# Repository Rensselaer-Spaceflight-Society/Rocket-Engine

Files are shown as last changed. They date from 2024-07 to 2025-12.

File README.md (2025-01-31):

# RPU Systems Design and Communications Protocol V1.1.0

> [!IMPORTANT]
> Last Updated: 10/8/2024

Below is a brief overview of the design and communications protocol between our laptop acting as our remote interface (i.e. the control room) and the Rocket Engine Test Stand itself.

## Table of Contents

- [Control Room](#control-room)
- [Test Stand Controller](#test-stand-controller)
- [Powering the Test Stand](#powering-the-test-stand)
- [Sensors](#sensors)
- [Valves](#valves)
- [Communications](#communications)
- [Command and Control](#command-and-control)
- [Sensor Data Transfer](#sensor-data-transfer)
- [Control Flow](#control-flow)
- [Arduino Pinout](#arduino-pinout)
- [Additional Info](#additional-info)

## Control Room

The software that remotely monitors the engine and allows us to send commands to the engine. This software is responsible for:

- Countdown
- Receiving and Saving Data
- Hold and Abort Signals
- Displaying the Data in a Human Friendly Way
  - Charts
  - Text Outputs
  - Color coding for if data is out of spec

### Technologies

We are using C++ and Qt 6.7.2 to build the control room software. You can install the Qt framework for Open Source Usage from https://www.qt.io/download-open-source.

## Test Stand Controller

The rocket engine controller is an Arduino based platform that controls the physical aspects of the rocket engine. This was the primary focus for the semester and is still the primary focus for this summer. This software is responsible for:

- Reading Sensors
- Opening and Closing Valves
- Sending Sensor Data back to the Control Room
- Ignition and Shutoff Sequence
- Processing Control Signals

## Powering the Test Stand

We have a variety of electronics that need power:

- Solenoid Valves, 48W (12vdc @4A)
- Arduino, 1W (12vdc @0.08333)
- Sensors, 5W (5v @1A)

The sensors need 5v, but everything else needs 12v, fortunately, the Arduino's power regulation will step the power down to 5v for the sensors.

Its really hard to send 60w @ 12vdc over 300ft, so we decided that battery power is our best bet for powering the test stand. Lithium Iron Phosphate (LiFePO4) batteries show the best potential for delivering both the voltage and current that the test stand will need.

The use of battery power allows us to set our downrange distance anywhere from 300ft (100m) - 3400ft (1000m).

### Technologies

This is built on the Arduino platform for easy and plentiful I/O. Arduino provides plenty of digital and analog pins for reading sensors and controlling valves. It also provides simple serial communications over UART.

> [!NOTE]
> Originally the rocket engine was supposed to be controlled via Raspberry Pi, we switched to the arduino platform for a couple reasons.
>
> - Setup is easier as there is no need to ssh into the arduino and run the control program, it starts up automatically on power on.
> - The Raspberry Pi has no Analog pin headers, the pressure transducers are analog sensors, switching to Arduino removes the need for analog-digital converters.
> - The Arduino takes less power, we can power it really easily via the VIN and GND pins compared to RasPI which is much harder to power
> - Arduino has first class support for our serial communications, where as raspberry pi has support but is slightly more difficult to implement
> - Arduino has no OS that is also has to run, it just runs our code and our code only.

## Sensors

The rocket engine has 8 sensors:

- 1 Load Cell for measuring thrust
- 4 Thermocouples
    - 1 At the Nozzle exit
    - 1 On the Kerosene Inlet and Injector Plate
    - 1 On the N2O inlet and injector Plate
    - On the combustion chamber at the throat of the nozzle (the constriction)
- 6 Pressure Transducers
  - 1 Inside the Combustion Chamber
    - According to David, the back of the combustion chamber should be cool enough to not destroy this sensor
  - 1 Down Line of the Inert Gas System
  - 2 Before the injector plate
    - 1 for fuel
    - 1 for oxidizer
  - 2 After the valves for fuel and oxidizer

The pressure transducers are analog sensors that vary their voltage depending on the pressure they are detecting.

The thermocouple and load cell both have amplifiers that act as analog-digital converters. The signals we take in will be digital signals. The thermocouple unfortunately does work on SPI (sorry Ashton).

## Valves

We are using three 12v solenoid valves that operate at 1.33 amps. This is simply too much power to send over a wire with our budget. See the power section for more information.

Power will be delivered to the solenoids via solid-state relays, this allows the
5v logic level of the Arduino power the relays reliably.

## Communications

The goal is to not be anywhere close to the engine when it is firing, the team is still deciding on an acceptable distance, but the current number is between 50 - 100m (170 - 340ft). To achieve this range with easy and reliable communications we are using UART serial communications via ethernet. This provides a well supported, and robust communication method.

> [!IMPORTANT]
> The Baud Rate for the serial communications has yet to be finalized, for testing we are using 9600 but this may change in the future.

Specifically the serial data will be converted to RS485 and sent over Cat 5 ethernet cable, this is supposedly an effective way to handle long range wired communication. [Source](https://electronics.stackexchange.com/questions/113188/long-distance-communication)

The Arduino's serial communication library automatically handles parity, start, and stop bits, so we don't need to handle this necessarily. The default is 8 data, 1 start and 1 stop bit with no parity, but we may be able to change this if needed.

Communications should be handled over the the Serial1 Port on the Arduino, Serial0 (aka just "Serial) is reserved for debugging via the Serial Monitor.

## Command and Control

The control room and the test stand use 64 bit (8 byte) signals to communicate different actions / states to each other the signals are as follows. When the test stand receives a command it should send an acknowledgement. If the control room fails to receive an acknowledgement it should reattempt sending the command up to **5** times. If after these
attempts there still is no acknowledgement, then the control room should assume connection
is lost and notify the user. If the test stand receives a command that it has already received then it should just send an acknowledgement instead of rerunning code.

If test stand connection is lost, then the test stand will automatically go into shutdown procedure.

The acknowledgement is just a repeat of the command received.

The following sequences are the different commands sent by the control computer and what
they tell the test stand to do.

- `CtrlActi` Control Computer Active, tells the test stand that a communication link is active.
- `LogStart` Tells the test stand to start the logging of sensor data and communicating that down the line.
- `InrtFlsh` Tells the test stand to perform an inert gas flush
- `PresFuel` Tells the test stand to open the pressure valve to the Kerosene
- `Ignition` Tells the test stand to open the valves and light the Steel Wool following the ignition protocol
- `Shutdown` Tells the test stand to close the oxidizer valve first, then the fuel valve.

On Shutdown, the test stand should send a message that the engine was shutdown.

## Sensor Data Transfer

Sensor data is sent in packets of 64 bytes of binary data with the following structure:

// The order of sensors is:
/*
 * thermocouple[0] = injector plate & kerosene inlet
 * thermocouple[1] = injector plate & oxidizer inlet
 * thermocouple[2] = outside the cc at the throat
 * thermocouple[3] = on the nozzle near the outlet
 *
 * pressureTransducer[0] = combustion chamber
 * pressureTransducer[1] = kerosene feed-line pressure
 * pressureTransducer[2] = kerosene tank pressure
 * pressureTransducer[3] = kerosene line pressure
 * pressureTransducer[4] = oxidizer tank pressure
 * pressureTransducer[5] = oxidizer line pressure
*/

```cpp
typedef struct
{
  char header[8] = "DataPack"; // Data recieved should be "DataPack" but cannot be assumed to be
  float loadCell;
  float thermocouple[4];
  float pressureTransducer[6];
  char checksum[12];
} SensorData;
```
The checksum is a 12-byte XOR hash that verifies all the data is solid and can be found below:

```cpp
void checksum12(void *checksum, const void *data, int n) {
    uint8_t* checksumPtr = (uint8_t *) checksum;
    const uint8_t* dataPtr = (uint8_t *) data;
    memset(checksum, 0, 12);
    for (int i = 0; i < n; ++i) {
        checksumPtr[i % 12] ^= dataPtr[i];
        checksumPtr[(i + 1) % 12] ^= (dataPtr[i] >> 4) | (dataPtr[i] << 4);  // Simple mixing
    }
}
```

## Control Flow

1. Test Stand comes online, sets up all the pins for the engine
1. Control Room comes online, and sends the `CtrlActi` signal while waiting for a `LogStart` signal
1. Control Room sends the `LogStart` signal, and the Test Stand begins sending Sensor Data every quarter second, and the `LogStart` signal.
1. Control Room sees the `LogStart` signal, and sends the `PressFuel` signal, which once seen by the Test Stand is sent back after the Fuel Tank is pressurized
1. Control Room sees the `PressFuel` signal, and sends the `InertFlush` signal, which once seen by the Test Stand is returned after a brief Inert Flush
1. Control Room sees the `InertFlush` signal and sends the `Ignite` signal, which once seen by the Test Stand is returned after the ignition sequence begins
1. After Ignition, the Test Stand sends sensor data as fast as it can for the duration of operation, whilst also checking if conditions are nominal
1. Assuming conditions are nominal, the Test Stand and the Control Room send the `Ping` Signal back and forth to ensure a stable connection.
1. If Conditions were unstable, there has been a significant amount of time since the Test Stand has received a `Ping`, or the Control Room has sent the `Shutdown` signal, the Test Stand intiates a Shutdown Sequence

## Arduino Pinout

See the Schematic using KiCad for the most up to date Arduino Pins.

## Additional Info

For additional info into how to build the Control Room software, configure the Arduino, and other parts of the project, consult the docs folder of the [GitHub Repository](https://github.com/Rensselaer-Spaceflight-Society/Rocket-Engine)

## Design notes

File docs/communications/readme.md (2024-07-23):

# RPU Systems Design and Communications Protocol V1.0.0

> [!IMPORTANT]
> Last Updated: 7/22/2024

Below is a brief overview of the design and communications protocol between our laptop acting as our remote interface (i.e. the control room) and the Rocket Engine Test Stand itself.

## Table of Contents
 - [Control Room](#control-room)
 - [Test Stand Controller](#test-stand-controller)
 - [Powering the Test Stand](#powering-the-test-stand)
 - [Sensors](#sensors)
 - [Valves](#valves)
 - [Communications](#communications)
 - [Command and Control](#command-and-control)
 - [Sensor Data Transfer](#sensor-data-transfer)
 - [Control Flow](#control-flow)
 - [Arduino Pinout](#arduino-pinout)
 - [Additional Info](#additional-info)

## Control Room

The software that remotely monitors the engine and allows us to send commands to the engine. This software is responsible for:

- Countdown
- Receiving and Saving Data
- Hold and Abort Signals
- Displaying the Data in a Human Friendly Way
    - Charts
    - Text Outputs
    - Color coding for if data is out of spec

### Technologies

All of these technologies are open for discussion, the main focus of systems this semester was the Rocket Engine side of things and developing systems to physically control the engine and read data. 

There may be an argument to switch to something like Python and use something like PyQt to do the GUI to make this cross-platform and possibly simplify development. As of right now this is the technology stack:

- C++ 
- x86-64 Linux (Ubuntu 22.04 but should work generally on most systems)
    - Linux makes C++ development and Serial port access easier
- FTXUI
    - A TUI (Terminal UI) for displaying data in a human readable fashion
- CMake for building the project and managing deps

## Test Stand Controller

The rocket engine controller is an Arduino based platform that controls the physical aspects of the rocket engine. This was the primary focus for the semester and is still the primary focus for this summer. This software is responsible for:

- Reading Sensors
- Opening and Closing Valves
- Sending Sensor Data back to the Control Room
- Ignition and Shutoff Sequence
- Processing Control Signals

## Powering the Test Stand

We have a variety of electronics that need power:

- Solenoid Valves, 48W (12vdc @4A)
- Arduino, 1W (12vdc @0.08333)
- Sensors, 5W (5v @1A)

The sensors need 5v, but everything else needs 12v, fortunately, the Arduino's power regulation will step the power down to 5v for the sensors.

Its really hard to send 60w @ 12vdc over 300ft, so we decided that battery power is our best bet for powering the test stand. Lithium Iron Phosphate (LiFePO4) batteries show the best potential for delivering both the voltage and current that the test stand will need.

The use of battery power allows us to set our downrange distance anywhere from 300ft (100m) - 3400ft (1000m).

### Technologies

This is built on the Arduino platform for easy and plentiful I/O. Arduino provides plenty of digital and analog pins for reading sensors and controlling valves. It also provides simple serial communications over UART.

> [!NOTE]
> Originally the rocket engine was supposed to be controlled via Raspberry Pi, we switched to the arduino platform for a couple reasons.
> - Setup is easier as there is no need to ssh into the arduino and run the control program, it starts up automatically on power on.
> - The Raspberry Pi has no Analog pin headers, the pressure transducers are analog sensors, switching to Arduino removes the need for analog-digital converters.
> - The Arduino takes less power, we can power it really easily via the VIN and GND pins compared to RasPI which is much harder to power
> - Arduino has first class support for our serial communications, where as raspberry pi has support but is slightly more difficult to implement
> - Arduino has no OS that is also has to run, it just runs our code and our code only.

## Sensors 

The rocket engine has 8 sensors:
- 1 Load Cell for measuring thrust
- 1 Thermocouple placed before the injector plate
- 6 Pressure Transducers
    - 1 Inside the Combustion Chamber
        - According to David, the back of the combustion chamber should be cool enough to not destroy this sensor
    - 1 Down Line of the Inert Gas System
    - 2 Before the injector plate
        - 1 for fuel
        - 1 for oxidizer
    - 2 After the valves for fuel and oxidizer

The pressure transducers are analog sensors that vary their voltage depending on the pressure they are detecting.

The thermocouple and load cell both have amplifiers that act as analog-digital converters. The signals we take in will be digital signals. The thermocouple unfortunately does work on SPI (sorry Ashton).

## Valves

We are using three 12v solenoid valves that operate at 1.33 amps. This is simply too much power to send over a wire with our budget. See the power section for more information.

Power will be delivered to the solenoids via solid-state relays, this allows the 
5v logic level of the Arduino power the relays reliably.

## Communications

The goal is to not be anywhere close to the engine when it is firing, the team is still deciding on an acceptable distance, but the current number is between 50 - 100m (170 - 340ft). To achieve this range with easy and reliable communications we are using UART serial communications via ethernet. This provides a well supported, and robust communication method.

> [!IMPORTANT]
> The Baud Rate for the serial communications has yet to be finalized, for testing we are using 9600 but this may change in the future.

Specifically the serial data will be converted to RS485 and sent over Cat 5 ethernet cable, this is supposedly an effective way to handle long range wired communication. [Source](https://electronics.stackexchange.com/questions/113188/long-distance-communication)

The Arduino's serial communication library automatically handles parity, start, and stop bits, so we don't need to handle this necessarily. The default is 8 data, 1 start and 1 stop bit with no parity, but we may be able to change this if needed.

Communications should be handled over the the Serial1 Port on the Arduino, Serial0 (aka just "Serial) is reserved for debugging via the Serial Monitor.

## Command and Control

The control room and the test stand use 64 bit (8 byte) signals to communicate different actions / states to each other the signals are as follows.

- Control Room Signals (sent from Control Room to Test Stand)
    - CtrlActi
        - Short for Control Room Active, sent as a response to the `TestActi` signal to indicate a connection between Control Room and Test Stand
    - LogStart
        - Short for Logging Start, indicates to the test stand to start reading and sending sensor data
    - InertGas
        - Triggers the Inert Gas Flush before / after firing
    - Ignition
        - Triggers the ignition and startup sequence
    - ShutDown
        - Triggers the shutdown sequence, closing the valves and performing an inert gas flush.
    - StopLogs
        - Tells the stand to terminate data logging, stops reading from the sensors and stops data transmission. The test stand must sent its `ShutDown` signal indicating the test stand is in the shutdown state.

- Test Stand Signals (sent from Test Stand to Control Room)
    - TestActi
        - Short for Test Stand Active, sent from the test stand once every second on test stand startup to indicate that the test stand is online and waiting for connection from the Control Room
    - CommsEst
        - Short for Communications Established, indicates that the Test Stand has received the Control Room's `CtrlActi` signal, and that a connection has been established.
    - InertFlw
        - Short for Inert Gas Flowing, indicates that the Test Stand is starting the Inert Gas flush.
    - InertStp
        - Short for Inert Gas Stop, indicates that the inert gas valves are closed, terminating the inert gas flush.
    - IgnStart
        - Short for Ignition Start, indicates that the test stand is attempting ignition of the engine.
    - HangFire
        - Indicates that there was no thrust produced or there was no oxidizer flow 1s after ignition so valves were automatically closed. Engine will start shutdown procedure.
    - AbrtFire
        - Short for Abort Fire, indicates some sensor is outside a safe window and fire is being aborted. Engine will start the shutdown procedure.
    - ShtDnRun
        - Short for Shutdown Running, indicates, that the test stand is running the shutdown procedure.
    - ShutDown
        - Sent after the test stand has shut all the valves and is done its shutdown procedure. The test stand will continue to send sensor data until it receives the `StopLogs` signal.
    - StopLogs
        - Sent as a response to the Control Room's `StopLogs` signal to indicate that the Test Stand is terminating logging.

## Sensor Data Transfer

Sensor data is sent in packets of 32 bytes (256 bits) of binary data with the following structure:

```cpp
typedef struct
{
  float loadCell;
  float thermocouple;
  float pressure[6];
} SensorData;
```

## Control Flow

1. Test Stand comes online, sets up all the pins for the engine, and starts sending the `TestActi` signal on the Serial1 port once every second.
1. Control Room comes online, and sends the `CtrlActi` signal, this signal will be sent again if the control room sees the `TestActi` signal again.
1. Test Stand sees the `CtrlActi` signal and responds with the `CommsEst` signal to indicate successful connection
1. The test stand will wait to start logging until it sees the `LogStart` signal from the control room. Upon receiving that signal, it will start reading from the sensors and sending data.
1. Upon receiving data, the control room will store that data into a CSV for later processing and then displaying that data in the chart
1. The control room will handle the countdown, performing an automatic hold at T-30s to allow us to perform 1 last check before ignition. 
    1. If we decide to continue with the countdown, the Control Room will send the `InertGas` signal at T-10s **(needs verification)** for an inert gas flush, and then send the `Ignition` at T-3s to ensure ignition is started by T-0s.
    1. If we decide to stop and abort, then the `ShutDown` signal is sent shutting down the test stand and ensuring all valves are closed.
1. On receive of the `InertGas` the Test Stand will respond with `InertFlw` and open the inert gas valves for some time **still to be decided**. Then after the valves are closed it will send an `InertStp` signal to indicate that the inert gas is done flowing.
1. On receiving the `Ignition` signal, the test stand will respond with `IgnStart` and then open fuel valve, ignite the igniter, and then open the oxidizer valve.
1. The test stand will monitor the sensors and will send either the `HangFire` signal if it detects a hang fire or `AbrtFire` signals if anything is outside the safe window.
1. If everything is ok, then ignition will continue until the fuel runs out, in which the `ShutDown` signal will be sent by the control room, the test stand will reply with `ShtDnRun` close valves, and perform any additional shutdown steps, then send its `ShutDown` signal.
1. Once the team is happy with the data collected, the `StopLogs` signal will be sent from the control room and the test stand will terminate its logging.

## Arduino Pinout

The Pinout is still being developed, the only finalized pins at the moment are:

- PIN 18: Output
    - Serial1 TX pin
- PIN 19: Input
    - Serial1 RX pin

## Additional Info

For additional info into how to build the Control Room software, configure the Arduino, and other parts of the project, consult the docs folder of the [GitHub Repository](https://github.com/Rensselaer-Spaceflight-Society/Rocket-Engine)

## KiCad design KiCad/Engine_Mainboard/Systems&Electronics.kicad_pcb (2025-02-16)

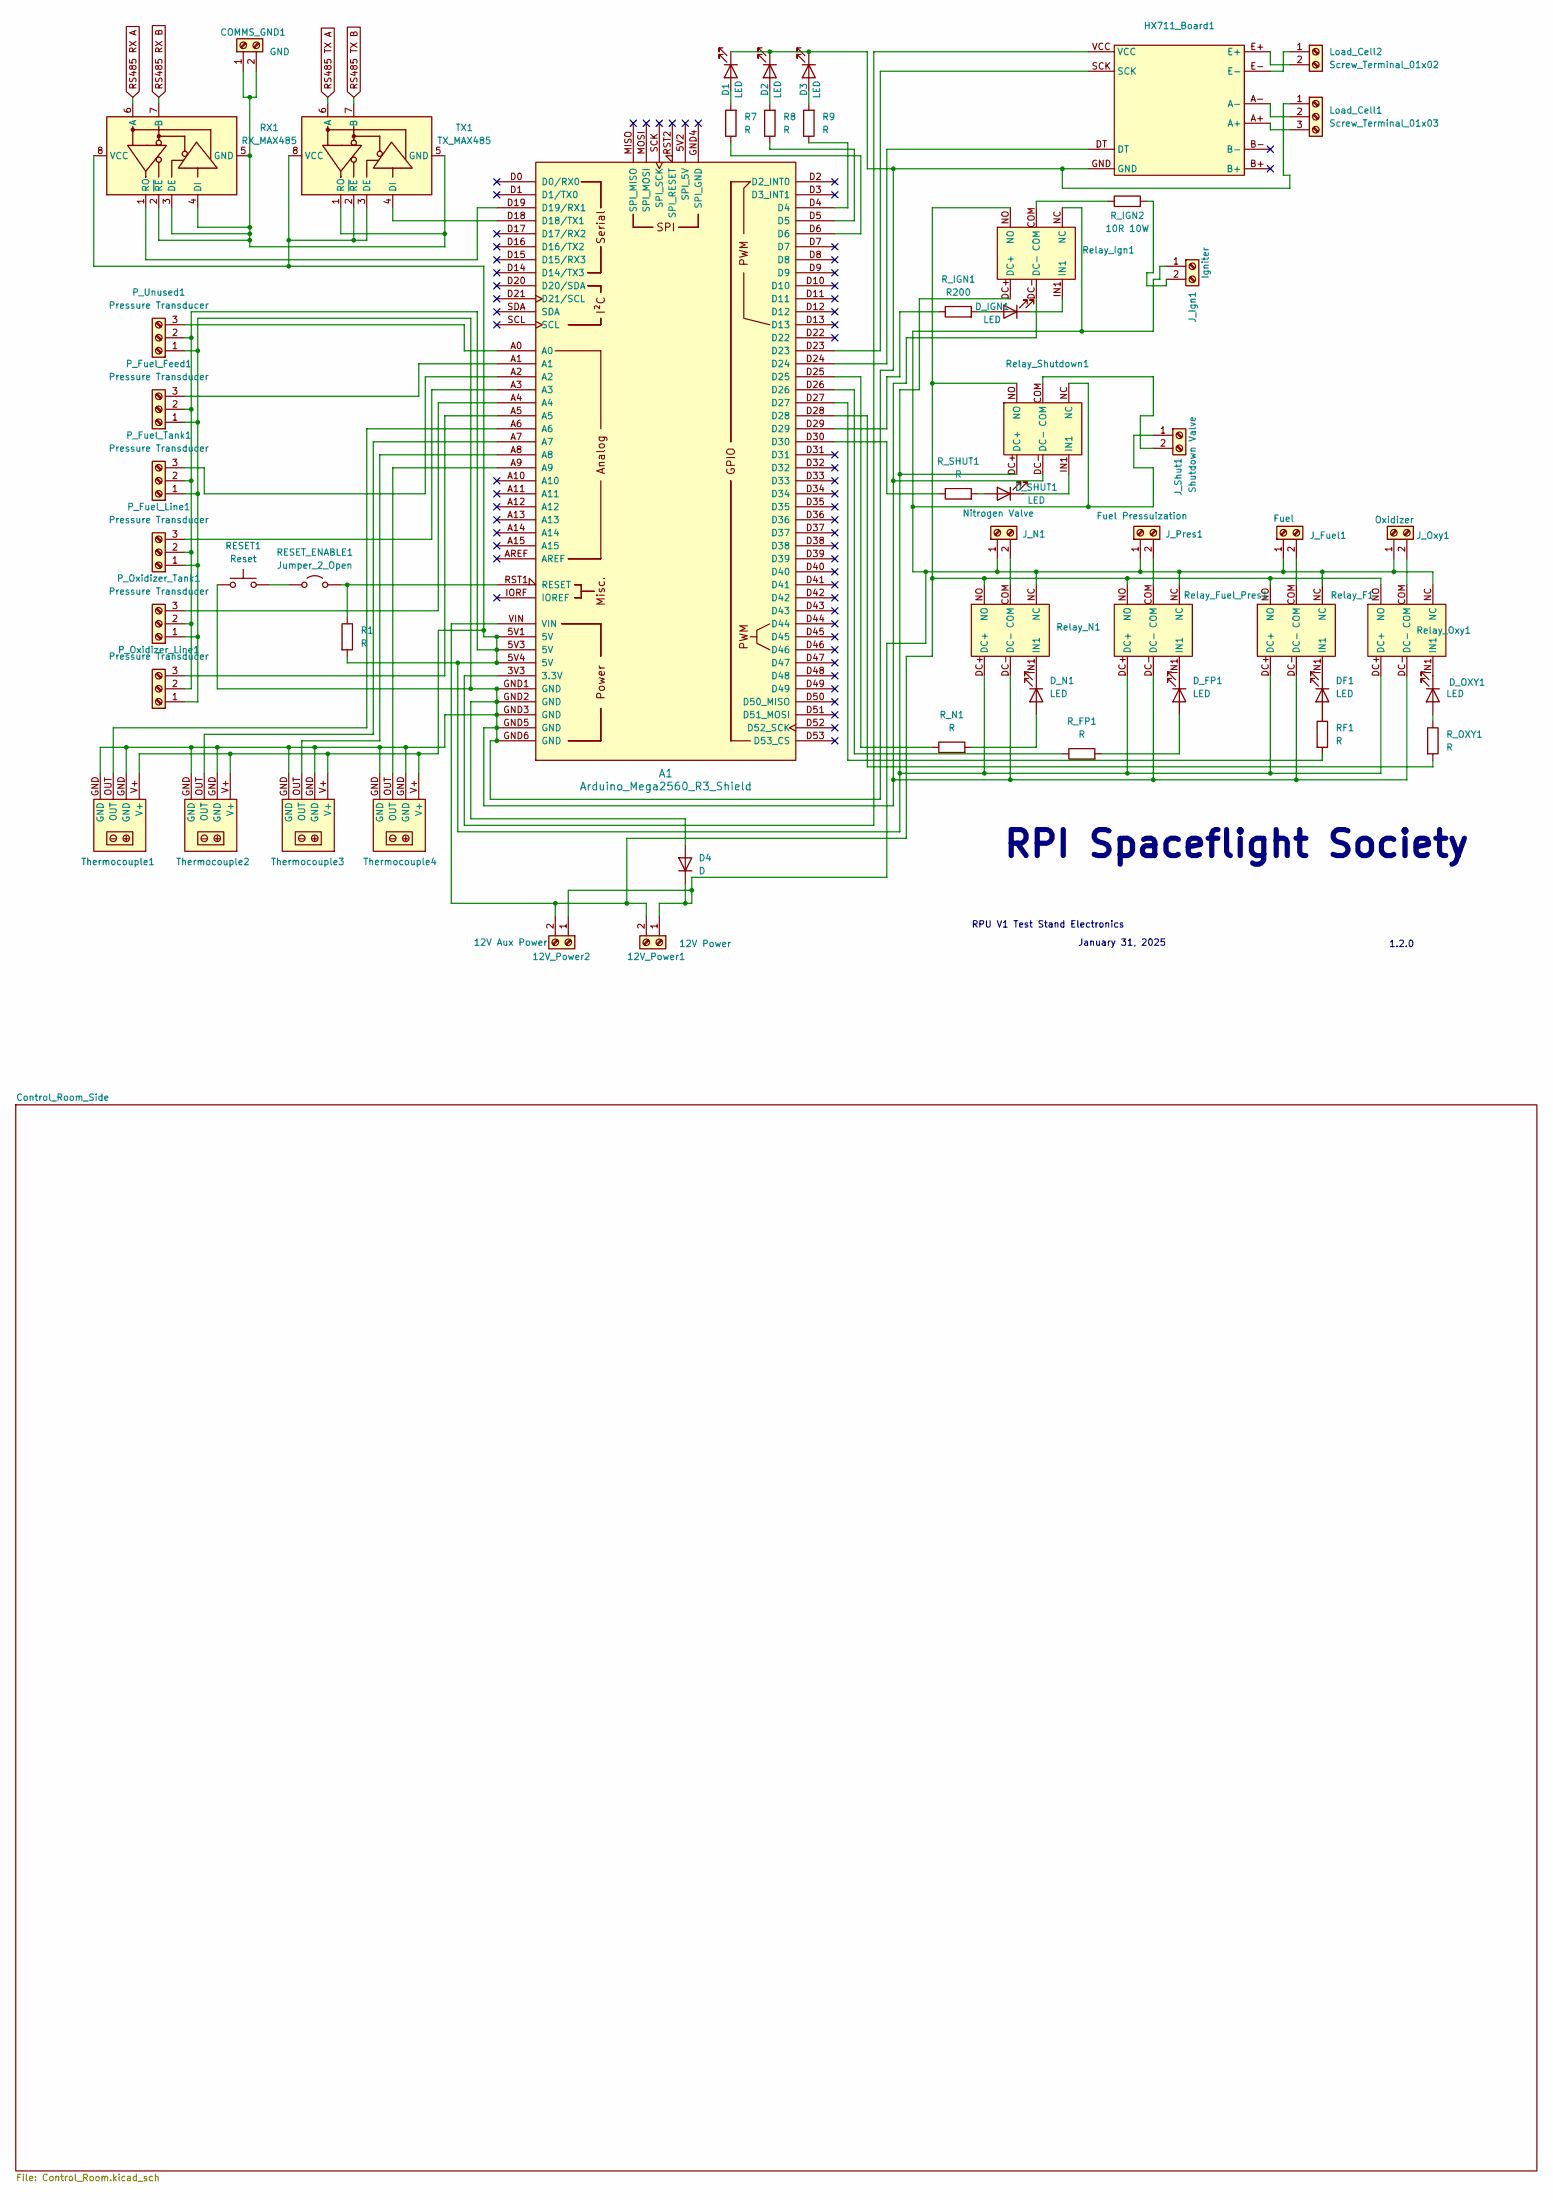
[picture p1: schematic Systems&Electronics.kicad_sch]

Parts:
12V_Power1: 12V Power; TerminalBlock_bornier-2_P5.08mm
12V_Power2: 12V Aux Power; TerminalBlock_bornier-2_P5.08mm
A1: Arduino_Mega2560_R3_Shield
COMMS_GND1: GND; TerminalBlock_bornier-2_P5.08mm
D1, D2, D3: LED; LED_D5.0mm
D4: D; D_A-405_P7.62mm_Horizontal
DF1: LED; LED_D5.0mm
D_FP1: LED; LED_D5.0mm
D_IGN1: LED; LED_D5.0mm
D_N1: LED; LED_D5.0mm
D_OXY1: LED; LED_D5.0mm
D_SHUT1: LED; LED_D5.0mm
HX711_Board1: HX711
J_Fuel1: Fuel; TerminalBlock_bornier-2_P5.08mm
J_Ign1: Igniter; TerminalBlock_bornier-2_P5.08mm
J_N1: Nitrogen Valve; TerminalBlock_bornier-2_P5.08mm
J_Oxy1: Oxidizer; TerminalBlock_bornier-2_P5.08mm
J_Pres1: Fuel Pressuization; TerminalBlock_bornier-2_P5.08mm
J_Shut1: Shutdown Valve; TerminalBlock_bornier-2_P5.08mm
Load_Cell1: Screw_Terminal_01x03; TerminalBlock_bornier-3_P5.08mm
Load_Cell2: Screw_Terminal_01x02; TerminalBlock_bornier-2_P5.08mm
P_Fuel_Feed1: Pressure Transducer; TerminalBlock_bornier-3_P5.08mm
P_Fuel_Line1: Pressure Transducer; TerminalBlock_bornier-3_P5.08mm
P_Fuel_Tank1: Pressure Transducer; TerminalBlock_bornier-3_P5.08mm
P_Oxidizer_Line1: Pressure Transducer; TerminalBlock_bornier-3_P5.08mm
P_Oxidizer_Tank1: Pressure Transducer; TerminalBlock_bornier-3_P5.08mm
P_Unused1: Pressure Transducer; TerminalBlock_bornier-3_P5.08mm
R1, R7, R8, R9: R; R_Axial_DIN0207_L6.3mm_D2.5mm_P7.62mm_Horizontal
RESET1: Reset; SW_PUSH_6mm
RESET_ENABLE1: Jumper_2_Open; PinHeader_1x02_P2.54mm_Vertical
RF1: R; R_Axial_DIN0207_L6.3mm_D2.5mm_P7.62mm_Horizontal
RX1: RX_MAX485; RS485_Transceiver
R_FP1: R; R_Axial_DIN0207_L6.3mm_D2.5mm_P7.62mm_Horizontal
R_IGN1: R200; R_Axial_DIN0207_L6.3mm_D2.5mm_P7.62mm_Horizontal
R_IGN2: 10R 10W; R_Axial_Power_L50.0mm_W9.0mm_P55.88mm
R_N1: R; R_Axial_DIN0207_L6.3mm_D2.5mm_P7.62mm_Horizontal
R_OXY1: R; R_Axial_DIN0207_L6.3mm_D2.5mm_P7.62mm_Horizontal
R_SHUT1: R; R_Axial_DIN0207_L6.3mm_D2.5mm_P7.62mm_Horizontal
Relay_F1: Relay
Relay_Fuel_Pres1: Relay
Relay_Ign1: Relay
Relay_N1: Relay
Relay_Oxy1: Relay
Relay_Shutdown1: Relay
TX1: TX_MAX485; RS485_Transceiver
Thermocouple1, Thermocouple2, Thermocouple3, Thermocouple4: AD8495

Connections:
unnamed: 12V_Power1.1, 12V_Power2.1, D4.1 (K), J_Fuel1.1, J_Ign1.1, J_N1.1, J_Oxy1.1, J_Pres1.1, J_Shut1.1, Relay_F1.NC, Relay_Fuel_Pres1.NC, Relay_Ign1.NC, Relay_N1.NC, Relay_Oxy1.NC, Relay_Shutdown1.NC
unnamed: 12V_Power1.2, 12V_Power2.2, A1.VIN, Relay_F1.NO, Relay_Fuel_Pres1.NO, Relay_Ign1.NO, Relay_N1.NO, Relay_Oxy1.NO, Relay_Shutdown1.NO
unnamed: A1.3V3 (3.3V), HX711_Board1.VCC
unnamed: A1.D18 (D18/TX1), TX1.4 (DI)
unnamed: A1.D19 (D19/RX1), RX1.1 (RO)
unnamed: A1.A6, Thermocouple1.OUT
unnamed: A1.A7, Thermocouple2.OUT
unnamed: A1.A8, Thermocouple3.OUT
unnamed: A1.A9, Thermocouple4.OUT
unnamed: A1.D4, R9.1
unnamed: A1.D5, R8.1
unnamed: A1.D6, R7.1
unnamed: A1.D23, HX711_Board1.SCK
unnamed: A1.D24, HX711_Board1.DT
unnamed: A1.D25, R_N1.1
unnamed: A1.D26, R_FP1.1
unnamed: A1.D27, RF1.2
unnamed: A1.D28, R_OXY1.2
unnamed: A1.D29, R_IGN1.1
unnamed: A1.D30, R_SHUT1.1
unnamed: A1.RST1 (RESET), R1.1, RESET_ENABLE1.2 (B)
unnamed: COMMS_GND1.1, COMMS_GND1.2, RX1.2 (~RE), RX1.3 (DE), RX1.4 (DI), RX1.5 (GND), TX1.1 (RO), TX1.5 (GND)
unnamed: D1.2 (A), R7.2
unnamed: A1.GND1 (GND), A1.GND2 (GND), A1.GND3 (GND), A1.GND5 (GND), A1.GND6 (GND), D1.1 (K), D2.1 (K), D3.1 (K), D4.2 (A), HX711_Board1.GND, Load_Cell1.1, P_Fuel_Feed1.1, P_Fuel_Line1.1, P_Fuel_Tank1.1, P_Oxidizer_Line1.1, P_Oxidizer_Tank1.1, P_Unused1.1, RESET1.1, Relay_F1.DC-, Relay_Fuel_Pres1.DC-, Relay_Ign1.DC-, Relay_N1.DC-, Relay_Oxy1.DC-, Relay_Shutdown1.DC-, Thermocouple1.GND, Thermocouple2.GND, Thermocouple3.GND, Thermocouple4.GND
unnamed: D2.2 (A), R8.2
unnamed: D3.2 (A), R9.2
unnamed: DF1.2 (A), RF1.1
unnamed: DF1.1 (K), Relay_F1.IN1
unnamed: D_FP1.2 (A), R_FP1.2
unnamed: D_FP1.1 (K), Relay_Fuel_Pres1.IN1
unnamed: D_IGN1.2 (A), R_IGN1.2
unnamed: D_IGN1.1 (K), Relay_Ign1.IN1
unnamed: D_N1.2 (A), R_N1.2
unnamed: D_N1.1 (K), Relay_N1.IN1
unnamed: D_OXY1.2 (A), R_OXY1.1
unnamed: D_OXY1.1 (K), Relay_Oxy1.IN1
unnamed: D_SHUT1.2 (A), R_SHUT1.2
unnamed: D_SHUT1.1 (K), Relay_Shutdown1.IN1
unnamed: J_Fuel1.2, Relay_F1.COM
unnamed: J_Ign1.2, R_IGN2.2
unnamed: J_N1.2, Relay_N1.COM
unnamed: J_Oxy1.2, Relay_Oxy1.COM
unnamed: J_Pres1.2, Relay_Fuel_Pres1.COM
unnamed: J_Shut1.2, Relay_Shutdown1.COM
unnamed: HX711_Board1.A-, Load_Cell1.2
unnamed: HX711_Board1.A+, Load_Cell1.3
unnamed: HX711_Board1.E-, Load_Cell2.1
unnamed: HX711_Board1.E+, Load_Cell2.2
unnamed: A1.5V1 (5V), A1.5V3 (5V), A1.5V4 (5V), P_Fuel_Feed1.2, P_Fuel_Line1.2, P_Fuel_Tank1.2, P_Oxidizer_Line1.2, P_Oxidizer_Tank1.2, P_Unused1.2, R1.2, RX1.8 (VCC), Relay_F1.DC+, Relay_Fuel_Pres1.DC+, Relay_Ign1.DC+, Relay_N1.DC+, Relay_Oxy1.DC+, Relay_Shutdown1.DC+, TX1.2 (~RE), TX1.3 (DE), TX1.8 (VCC), Thermocouple1.V+, Thermocouple2.V+, Thermocouple3.V+, Thermocouple4.V+
unnamed: A1.A1, P_Fuel_Feed1.3
unnamed: A1.A3, P_Fuel_Line1.3
unnamed: A1.A2, P_Fuel_Tank1.3
unnamed: A1.A5, P_Oxidizer_Line1.3
unnamed: A1.A4, P_Oxidizer_Tank1.3
unnamed: A1.A0, P_Unused1.3
unnamed: RESET1.2, RESET_ENABLE1.1 (A)
unnamed: R_IGN2.1, Relay_Ign1.COM
RS485 RX A: RX1.6 (A)
RS485 RX B: RX1.7 (B)
RS485 TX A: TX1.6 (A)
RS485 TX B: TX1.7 (B)

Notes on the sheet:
RPU V1 Test Stand Electronics
RPI Spaceflight Society
January 31, 2025
1.2.0

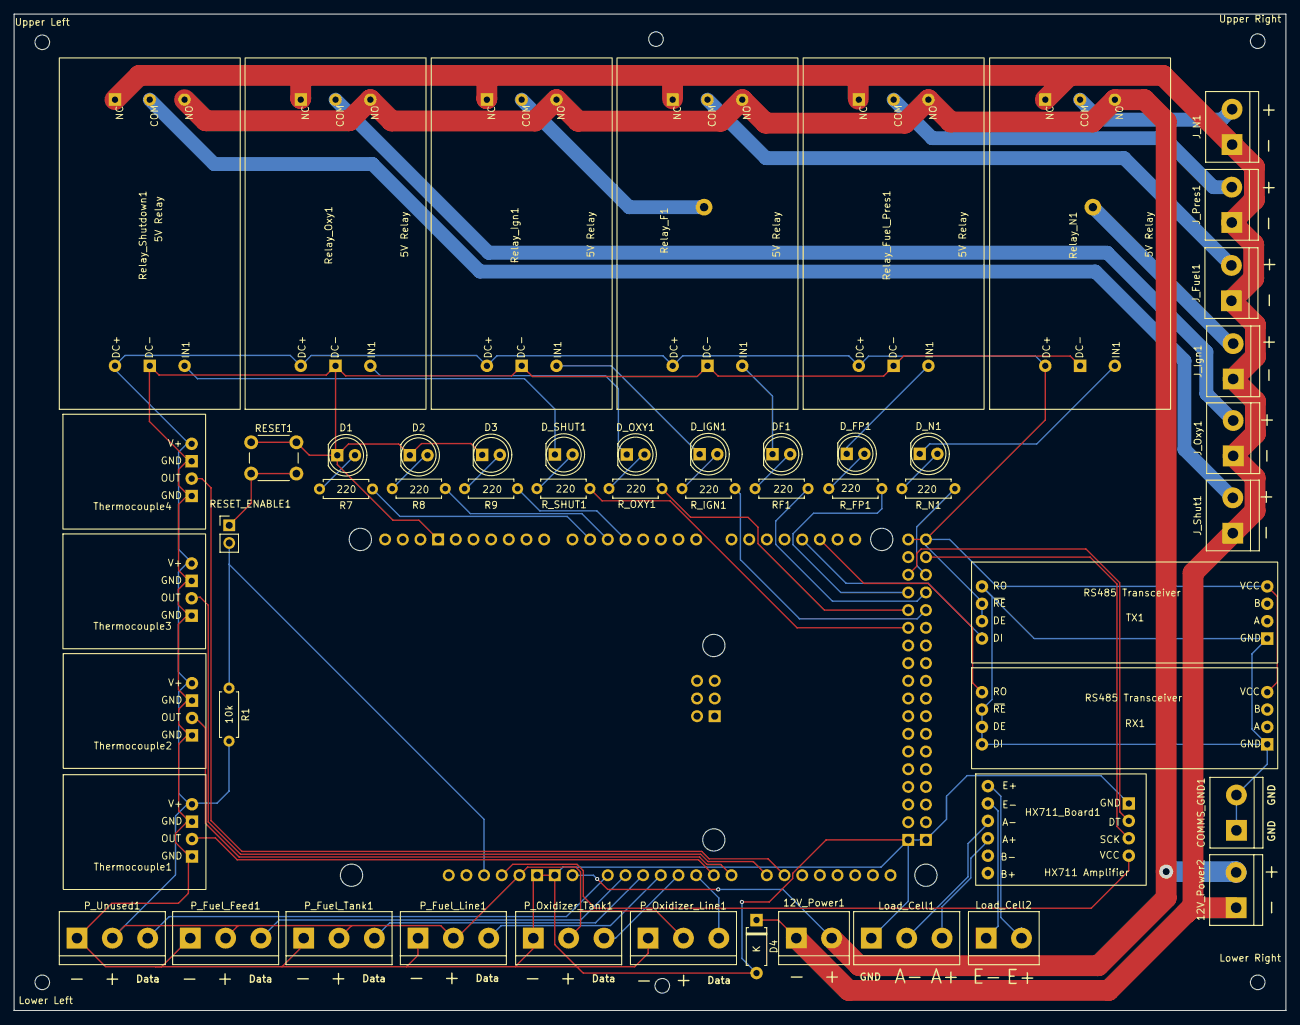
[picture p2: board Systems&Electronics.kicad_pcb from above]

Board: 2 copper layers, 182.8 x 143.2 mm, 58 parts (1 on the bottom side), 57 nets.

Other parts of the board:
Lower Left: MountingHole_2.1mm
Lower Right: MountingHole_2.1mm
Upper Left: MountingHole_2.1mm
Upper Right: MountingHole_2.1mm

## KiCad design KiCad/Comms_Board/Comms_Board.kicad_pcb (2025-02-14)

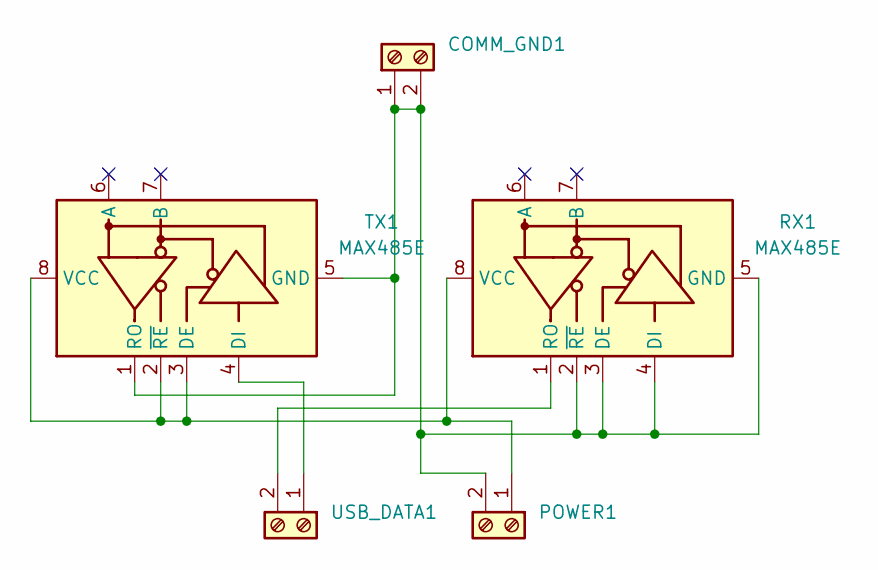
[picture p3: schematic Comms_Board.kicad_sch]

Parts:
COMM_GND1: Screw_Terminal_01x02; TerminalBlock_bornier-2_P5.08mm
POWER1: Screw_Terminal_01x02; TerminalBlock_bornier-2_P5.08mm
RX1: MAX485E; RS485_Transceiver
TX1: MAX485E; RS485_Transceiver
USB_DATA1: Screw_Terminal_01x02; TerminalBlock_bornier-2_P5.08mm

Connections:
unnamed: COMM_GND1.1, COMM_GND1.2, POWER1.2, RX1.2 (~RE), RX1.3 (DE), RX1.4 (DI), RX1.5 (GND), TX1.1 (RO), TX1.5 (GND)
unnamed: POWER1.1, RX1.8 (VCC), TX1.2 (~RE), TX1.3 (DE), TX1.8 (VCC)
unnamed: RX1.1 (RO), USB_DATA1.2
unnamed: TX1.4 (DI), USB_DATA1.1

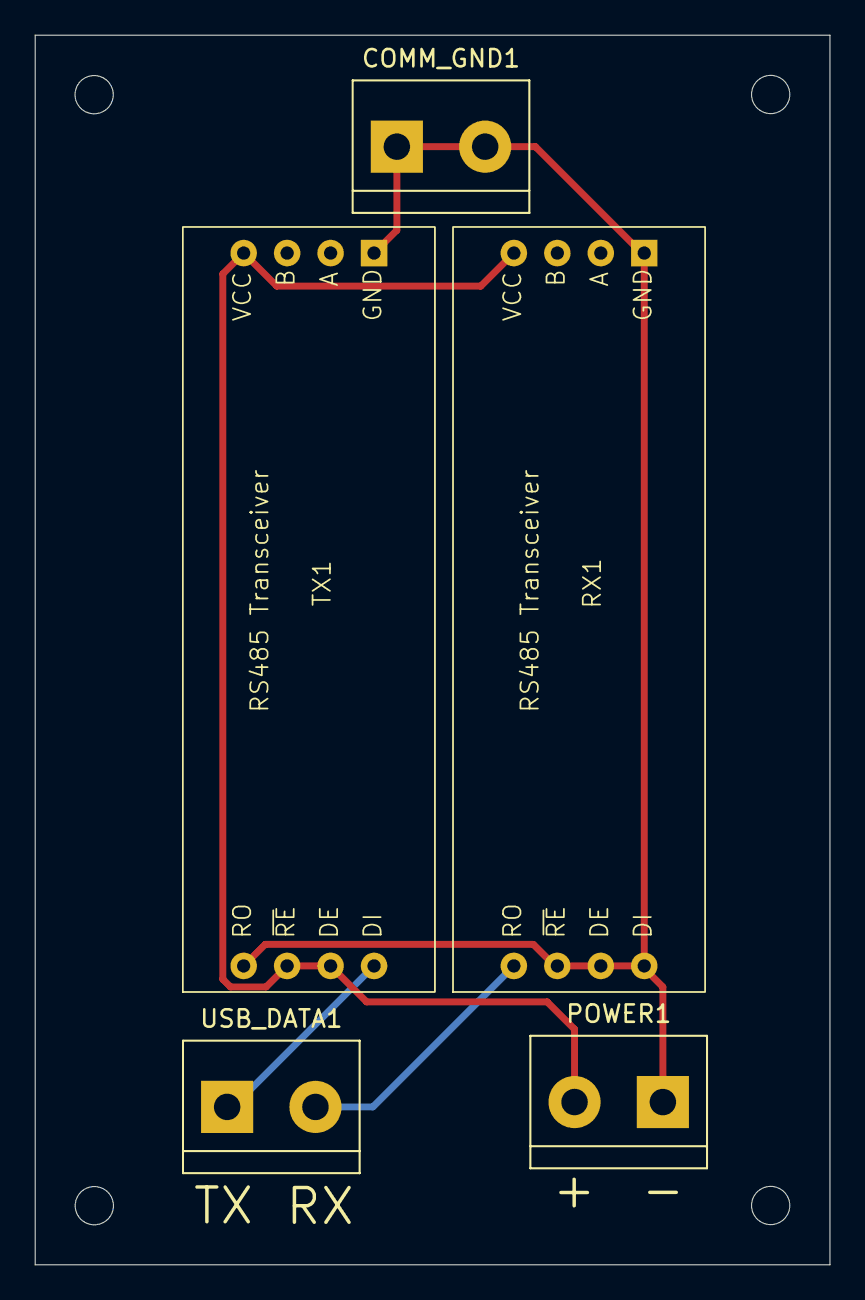
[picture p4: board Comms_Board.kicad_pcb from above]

Board: 2 copper layers, 45.7 x 70.7 mm, 5 parts (0 on the bottom side), 4 nets.

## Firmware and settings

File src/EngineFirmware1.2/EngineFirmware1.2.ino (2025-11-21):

#define PRODUCTION false
#define ENABLE_LOGGING true
#define READ_SENSORS true
#define ENABLE_PINGS false

#if PRODUCTION
#define BAUD_RATE 38400
#define ENABLE_LOGGING true  // Production should always have logging enabled
#define ENABLE_PINGS true    // Production should always have pings
#define READ_SENSORS true    // Production should always read from sensors
#define SerialPort Serial1   // Use the production serial pins
#else
#define BAUD_RATE 76800
#define SerialPort Serial1  // Use the USB port for debugging
#endif

#include "commands.h"
#include "pins.h"
#include "sensors.h"
#include <Servo.h>

char dataIn[COMMAND_SIZE_BYTES + 1];
EngineStates currentState = EngineStates::NO_CONNECTION;
unsigned int lastPingTime = 0;
unsigned int lastEventTime = 0;
int commandRepeats = 0;

uint64_t lastDataTransmissionTime = 0;


void setup() {
  Serial.begin(9600);
  SerialPort.begin(BAUD_RATE);
  while (!SerialPort) {
    ;
  }
  setupPins();
  Serial.println("Setup Resetting Pins");
  resetPins();
  lastPingTime = millis();
  srand(analogRead(15));
}

void loop() {
  // Handle any incomming commands
  if (SerialPort.available() >= COMMAND_SIZE_BYTES) {
    SerialPort.readBytes(dataIn, COMMAND_SIZE_BYTES);
    // SerialPort.println(SerialPort.available());
    dataIn[COMMAND_SIZE_BYTES] = 0; // Null Terminator
    handleCommand(dataIn, currentState, lastPingTime, lastEventTime, commandRepeats);
  }

  // Read Sensor Data, Send it back, and validate it
  if (currentState >= EngineStates::LOG_START && currentState != EngineStates::SHUTDOWN_CONFIRMED && ENABLE_LOGGING) {
    uint64_t currentTime = millis();
    if ((currentTime - lastDataTransmissionTime) >= MINIMUM_DATA_TRANSMIT_TIME_MS) {
      readSensorData(sensorData);
      sendSensorData(sensorData);
      lastDataTransmissionTime = currentTime;
    }
  }

  // If we should be validating data, then start validating that data
  if (currentState >= EngineStates::FUEL_PRESSURIZATION && currentState < EngineStates::SHUTDOWN_NITROGEN_FLUSH_STARTED && ENABLE_LOGGING) {
    if (!nominalDataCheck(sensorData)) {
      startShutdown();
      currentState = EngineStates::SHUTDOWN_NITROGEN_FLUSH_STARTED;
      lastEventTime = millis();
      SerialPort.write(SHUTDOWN, COMMAND_SIZE_BYTES);
      SerialPort.flush();
    }
  }

  // Handle Lost Connection
  if (commandRepeats > MAX_COMMAND_REPEATS) {
    if (currentState >= EngineStates::OXIDIZER_OPEN) {
      startShutdown();
      lastEventTime = millis();
      commandRepeats = 0;
      currentState = EngineStates::CONNECTION_LOST;
      SerialPort.write(CONNECTION_LOST, COMMAND_SIZE_BYTES);
      SerialPort.flush();
    } else {
      Serial.println("Max Repeat Resetting Pins");
      resetPins();

      SerialPort.write(CONNECTION_LOST, COMMAND_SIZE_BYTES);
      SerialPort.flush();
      digitalWrite(LED3, HIGH);
      currentState = EngineStates::NO_CONNECTION;
    }
  }

  // Check for pings
  if (currentState >= EngineStates::CONNECTION_ESTABLISHED && ENABLE_PINGS) {
    int currentTime = millis();
    // If there has been too much time between pings, then attempt shutting down.
    if ((currentTime - lastPingTime) > MAX_PING_DELAY_MS) {
      if (currentState >= EngineStates::OXIDIZER_OPEN) {
        startShutdown();
        lastEventTime = millis();
        commandRepeats = 0;
        currentState = EngineStates::CONNECTION_LOST;
        SerialPort.write(CONNECTION_LOST, COMMAND_SIZE_BYTES);
        SerialPort.flush();
      } else {
        Serial.println("Pings Lost Resetting Pins");
        resetPins();
        SerialPort.write(CONNECTION_LOST, COMMAND_SIZE_BYTES);
        SerialPort.flush();
        digitalWrite(LED3, HIGH);
        currentState = EngineStates::NO_CONNECTION;
      }
    }
  }

  // Handle any multi-step commands (inert flush, ignition, shutdown)

  // Handling finishing the pre-burn inert flush
  if (currentState == EngineStates::PRE_BURN_NITROGEN_FLUSH_STARTED) {
    int currentTime = millis();
    if ((currentTime - lastEventTime) > NITROGEN_FLUSH_DELAY_MS) {
      closeValve(NITROGENVALVE);
      currentState = EngineStates::PRE_BURN_NITROGEN_FLUSH_FINISHED;
      SerialPort.write(NITROGEN_FLUSH_FINISHED, COMMAND_SIZE_BYTES);
      SerialPort.flush();
    }
  }

  // Handling lighting the igniter after fuel flow
  if (currentState == EngineStates::OXIDIZER_OPEN) {
    int currentTime = millis();
    if ((currentTime - lastEventTime) > FUEL_VALVE_OPEN_DELAY_MS) {
      openValve(IGNITERVALVE);
      openValve(FUELVALVE);
      currentState = EngineStates::IGNITION;
      lastEventTime = millis();
    }
  }

  // Handle the Shutdown Inert Flush
  if (currentState == EngineStates::SHUTDOWN_NITROGEN_FLUSH_STARTED) {
    int currentTime = millis();
    if ((currentTime - lastEventTime) > NITROGEN_FLUSH_DELAY_MS) {
      closeValve(NITROGENVALVE);
      currentState = EngineStates::SHUTDOWN_CONFIRMED;
      SerialPort.write(SHUTDOWN_CONFIRMED, COMMAND_SIZE_BYTES);  // Indicate to the control computer the shutdown is done
      SerialPort.flush();
      digitalWrite(LED1, HIGH);
    }
  }

  // Handle the Shutdown Inert Flush when connection is lost
  if (currentState == EngineStates::CONNECTION_LOST) {
    int currentTime = millis();
    if ((currentTime - lastEventTime) > NITROGEN_FLUSH_DELAY_MS) {
      closeValve(NITROGENVALVE);
      currentState = EngineStates::NO_CONNECTION;
      SerialPort.write(SHUTDOWN_CONFIRMED, COMMAND_SIZE_BYTES);  // Indicate to the control computer the shutdown is done
      SerialPort.flush();
      digitalWrite(LED3, HIGH);
    }
  }
}

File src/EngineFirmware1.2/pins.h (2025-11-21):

#include "Arduino.h"
#ifndef __PINS_H_
#define __PINS_H_
#include "HX711.h"
#include <Servo.h>

// Pin Values (Digital)
constexpr int NITROGENVALVE = 28;
constexpr int PRESFUELVALVE = 26;
constexpr int FUELVALVE = 27;
constexpr int OXIDIZERVALVE = A0;
constexpr int IGNITERVALVE = 29;
constexpr int SHUTDOWN_VALVE = 30;

// Analog Pins for Pressure Transducers
// constexpr int PRESSSEN1 = A0;
constexpr int PRESSSEN2 = A1;
constexpr int PRESSSEN3 = A2;
constexpr int PRESSSEN4 = A3;
constexpr int PRESSSEN5 = A4;
constexpr int PRESSSEN6 = A5;

// Digital Pin for Load Cell
constexpr int LOADCELL = 24;

//SCK Pin for Load Cell
constexpr int LOADCELL_SCK = 23;

//Creating scale object for Load Cell
HX711 scale;
Servo oxidizerValve;


// Thermocouple Analog Pins
constexpr int THERMOCPL1 = A6;
constexpr int THERMOCPL2 = A7;
constexpr int THERMOCPL3 = A8;
constexpr int THERMOCPL4 = A9;

// LED Ports (Digital)
constexpr int LED1 = 6;
constexpr int LED2 = 5;
constexpr int LED3 = 4;

void setupPins() {
  pinMode(OXIDIZERVALVE, OUTPUT);
  digitalWrite(OXIDIZERVALVE, LOW);
  scale.begin(LOADCELL, LOADCELL_SCK);
  pinMode(PRESSSEN2, INPUT);
  pinMode(PRESSSEN3, INPUT);
  pinMode(PRESSSEN4, INPUT);
  pinMode(PRESSSEN5, INPUT);
  pinMode(PRESSSEN6, INPUT);
  pinMode(THERMOCPL1, INPUT);
  pinMode(THERMOCPL2, INPUT);
  pinMode(THERMOCPL3, INPUT);
  pinMode(THERMOCPL4, INPUT);

  pinMode(NITROGENVALVE, OUTPUT);
  pinMode(FUELVALVE, OUTPUT);
  pinMode(IGNITERVALVE, OUTPUT);
  pinMode(PRESFUELVALVE, OUTPUT);
  pinMode(SHUTDOWN_VALVE, OUTPUT);
  pinMode(LED1, OUTPUT);
  pinMode(LED2, OUTPUT);
  pinMode(LED3, OUTPUT);
  Serial.println("Setup Pins");
}

void resetPins() {
  Serial.println("Resetting Pins. ");
  digitalWrite(OXIDIZERVALVE, LOW);
  digitalWrite(NITROGENVALVE, LOW);
  digitalWrite(FUELVALVE, LOW);
  digitalWrite(IGNITERVALVE, LOW);
  digitalWrite(PRESFUELVALVE, LOW);
  digitalWrite(LED1, LOW);
  digitalWrite(LED2, LOW);
  digitalWrite(LED3, LOW);
}

#endif  // __PINS_H_

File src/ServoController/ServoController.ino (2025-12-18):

#include<Servo.h>

#define OXIDIZER_VALVE_SERVO_PIN 8
#define OXIDIZER_VALVE_OPEN_POSITION 10
#define OXIDIZER_VALVE_CLOSED_POSITION 105;
#define SERVO_STATUS_PIN 3

Servo oxidizer_valve;

void setup() {
  oxidizer_valve.attach(OXIDIZER_VALVE_SERVO_PIN);
  pinMode(SERVO_STATUS_PIN, INPUT);
}

void loop() {
  // If Servo Status Pin is High then we open the valve, otherwise close it
  if (digitalRead(SERVO_STATUS_PIN)){
    oxidizer_valve.write(OXIDIZER_VALVE_OPEN_POSITION);
  }else{
    oxidizer_valve.write(OXIDIZER_VALVE_CLOSED_POSITION);
  }
}

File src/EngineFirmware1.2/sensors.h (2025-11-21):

#include <stdlib.h>
#include "Arduino.h"

#ifndef __SENSORS_H_
#define __SENSORS_H_

#include "pins.h"
#include "HX711.h"

constexpr float voltageToTempScale = 0.005;
constexpr float PSItoKPaFactor = 6.89476;
constexpr char HEADER[] = "DataPack";

#define MINIMUM_DATA_TRANSMIT_TIME_MS 0

typedef struct sensors_struct {
  char header[8];
  float loadCell;
  float thermocouple[4];
  float pressure[6];
  char checkSum[12];
} Sensors;

float processThermocoupleValue(int analogSignal) {
  float voltage = analogSignal * (5.0 / 1023.0);
  return voltage / voltageToTempScale;  // Convert to Celsius
}

float read_loadcell(HX711 &scale) {
  static float load_cell = 0;
  
  if (scale.is_ready()) {
    load_cell = ((float)(scale.read() + 2383.0) / 904.0 - 10);
  }

  return load_cell;
}

float processPressureValue(int analogSignal) {
  // 0.5v -> 0 PSI
  // 4.5v -> 500 PSI
  float voltage = analogSignal * (5.0 / 1023.0);
  float psi = (voltage - 0.5) * (500 / 4.0);  // Convert to PSI
  return psi;
}

void checksum12(void *checksum, const void *data, int n) {
  unsigned char *checksumPtr = (unsigned char *)checksum;
  const unsigned char *dataPtr = (unsigned char *)data;
  memset(checksumPtr, 0, 12);
  for (int i = 0; i < n; ++i) {
    checksumPtr[i % 12] ^= dataPtr[i];
    checksumPtr[(i + 1) % 12] ^= (dataPtr[i] >> 4) | (dataPtr[i] << 4);
  }
}


#if READ_SENSORS
void readSensorData(Sensors &sensorData) {
  // Copy the data header to the struct
  memcpy(&sensorData.header, HEADER, 8);

  sensorData.loadCell = read_loadcell(scale);

  sensorData.pressure[0] = 0; // This sensor is unused and so we always return 0.
  sensorData.pressure[1] = processPressureValue(analogRead(PRESSSEN2));
  sensorData.pressure[2] = processPressureValue(analogRead(PRESSSEN3));
  sensorData.pressure[3] = processPressureValue(analogRead(PRESSSEN4));
  sensorData.pressure[4] = processPressureValue(analogRead(PRESSSEN5));
  sensorData.pressure[5] = processPressureValue(analogRead(PRESSSEN6));

  sensorData.thermocouple[0] = processThermocoupleValue(analogRead(THERMOCPL1));
  sensorData.thermocouple[1] = processThermocoupleValue(analogRead(THERMOCPL2));
  sensorData.thermocouple[2] = processThermocoupleValue(analogRead(THERMOCPL3));
  sensorData.thermocouple[3] = processThermocoupleValue(analogRead(THERMOCPL4));

  // Compute the checksum for the sensor data
  checksum12(&sensorData.checkSum, &sensorData, 52);
}
#else
// If we are not reading from sensors, we should fudge a bunch of random data from 1-21
void readSensorData(Sensors &sensorData) {
  // Copy the data header to the struct
  memcpy(&sensorData.header, HEADER, 8);

  // TODO: Handle reading from the Load Cell
  sensorData.loadCell =  ((float) rand()) / RAND_MAX * 20 + 1;

  sensorData.pressure[0] =  0;
  sensorData.pressure[1] =  ((float) rand()) / RAND_MAX * 20 + 1;
  sensorData.pressure[2] =  ((float) rand()) / RAND_MAX * 20 + 1;
  sensorData.pressure[3] =  ((float) rand()) / RAND_MAX * 20 + 1;
  sensorData.pressure[4] =  ((float) rand()) / RAND_MAX * 20 + 1;
  sensorData.pressure[5] =  ((float) rand()) / RAND_MAX * 20 + 1;

  sensorData.thermocouple[0] =  ((float) rand()) / RAND_MAX * 20 + 1;
  sensorData.thermocouple[1] =  ((float) rand()) / RAND_MAX * 20 + 1;
  sensorData.thermocouple[2] =  ((float) rand()) / RAND_MAX * 20 + 1;
  sensorData.thermocouple[3] =  ((float) rand()) / RAND_MAX * 20 + 1;

  // Compute the checksum for the sensor data
  checksum12(&sensorData.checkSum, &sensorData, 52);
}
#endif


// TODO: Implement
bool nominalDataCheck(Sensors &sensorData) {
  return true;
}


#endif

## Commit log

2024-01-14 Scrapping Arduino, Moving to Raspberry Pi, Also Switching to wired comms
2024-02-17 Ok I might need to switch build systems to be able to use FTXUI
2024-02-17 Switching to CMake
2024-04-20 migrating to the arduino platform for control
2024-08-07 Adding unfinished schematics
    [Systems&Electronics.kicad_pcb, Systems&Electronics.kicad_sch]
2024-08-07 V1 Systems Schematics
    [Systems&Electronics.kicad_sch]
2024-08-08 Electronics Schematic V1.1.0
    [Systems&Electronics.kicad_sch]
2024-08-27 Updating the arduino program to match implementation details
2024-09-05 Adding Igniter to Schematic
    [Systems&Electronics.kicad_sch]
2024-09-11 fix: Adding Resistors, Capacitors, and Diodes to Schematic - Also rerouted 12v ground to not run through the Arduino
    [Systems&Electronics.kicad_sch]
2024-09-11 Add the Control Room Side of the Signal Decode
    [Control_Room.kicad_sch, Systems&Electronics.kicad_sch]
2024-09-11 feat: Add the Control Room Side Signal Decoder
    [Control_Room.kicad_sch, Systems&Electronics.kicad_sch]
2024-09-22 Update the docs with the new control flow
2024-10-05 Added the receive thread and the sending threads.
2024-10-06 Added fourth solenoid and associated timer, fixed com lines, added three test LEDs
    [Systems&Electronics.kicad_sch]
2024-10-13 Thermocouples
    I added thermocouples to the systems schematic.
    [Systems&Electronics.kicad_pcb, Systems&Electronics.kicad_sch]
2024-10-13 Update Systems&Electronics.kicad_sch
    Revised version of the added thermocouples
    [Systems&Electronics.kicad_sch]
2024-10-13 Added timer function that updates the command list every 200msec
2024-10-15 feat(comms): integrate serial writer into main thread
2024-10-20 fix(schematics): remove shorts in pressure transducers
    [Systems&Electronics.kicad_sch]
2024-10-20 fixed the 4th solenoid
    [Systems&Electronics.kicad_sch]
2024-10-20 add Leds
    [Systems&Electronics.kicad_sch]
2024-10-20 Update Schematic to remove unneeded caps and resistors
    [Control_Room.kicad_sch, Systems&Electronics.kicad_sch]
2024-10-25 feat(comms): error handling and worker mainloop
    [serialworker.h]
2024-11-05 Timer now shows minutes, seconds, and millisecs
2024-11-05 has new function that allows pausing timer
2024-11-05 Timer pauses at 30 seconds
2024-11-05 feat(GUI): data logging fix, user alerts, and minor refactor of connections
    [mainwindow.h]
2024-11-05 fix(GUI): update the names of the chart to adjust for the new sensor placement
2024-12-20 updating firmware and schematics to be consistent
    [Systems&Electronics.kicad_sch]
2024-12-21 Firmware Refactor (Untested)
    [Systems&Electronics.kicad_sch]
2025-01-02 Implemented FSM for handling engine state.
    TODO:
    - Ability to create new log files when the test is restarted
    - Clearing the graphs when a test is restarted
    - QT Signal and Slot Connections
    - Debugging
2025-01-06 minor bug fixes
    The arduino is not responding to the commands despite the RX LED
    lighting up.
    [serialworker.h]
2025-01-14 Fixing Bugs with Comms
    - Slowly making progress still lots to fix
    [serialworker.h]
2025-01-23 Fix a bunch of software and firmware bugs :)
    [commands.h, serialworker.h]
2025-01-26 Add PCB Footprints
2025-01-31 Adding Relay Footprint
2025-01-31 feat(GUI) Command Reader/Writer Implementation and Starting PCB
    * feat(GUI): starting coms)
    * feat(comms): serial writer implementation v1
    * feat(comms): integrate serial writer into main thread
    * feat(comms): shutdown logic added
    * Command Writer v2
    * feat(comms): data send is partially working
    * feat(comms): Serial Command Writer v4 started
    * feat(comms): error handling and worker mainloop
    * feat(comms): error handling and worker mainloop
    * feat(comms): Serial Communications system v4 done
    Needs to be connected to the main file properly
    Needs to be tested
    * feat(GUI): minor fixes
    * feat(GUI): starting log handler
    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
    [Systems&Electronics.kicad_sch]
2025-02-02 PCB Layout V1
    [Control_Room.kicad_sch, Systems&Electronics.kicad_pcb, Systems&Electronics.kicad_sch]
2025-02-09 PCB layout minor updates
    [Systems&Electronics.kicad_pcb, Systems&Electronics.kicad_sch]
2025-02-09 Footprint and PCB updates
    [Systems&Electronics.kicad_pcb, Systems&Electronics.kicad_sch]
2025-02-10 PCB design reorg
    [Comms_Board.kicad_pcb, Comms_Board.kicad_sch, Control_Room.kicad_sch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]
2025-02-10 PCB Ignition Resistor Move
    [Systems&Electronics.kicad_pcb, Systems&Electronics.kicad_sch]
2025-02-10 PCB minor trace move
    [Systems&Electronics.kicad_pcb]
2025-02-10 feat(PCB): PCB V1.1.0 (#14)
    * PCB Layout V1
    * PCB layout minor updates
    * Footprint and PCB updates
    * PCB design reorg
    * PCB Ignition Resistor Move
    * PCB minor trace move
    [Comms_Board.kicad_pcb, Comms_Board.kicad_sch, Control_Room.kicad_sch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]
2025-02-13 Finishing touches, added redundant power terminals, and reset button.
    [Control_Room.kicad_sch, Systems&Electronics.kicad_pcb, Systems&Electronics.kicad_sch]
2025-02-13 feat(PCB): update PCB organization, add reset button (#15)
    * Finishing touches, added redundant power terminals, and reset button.
    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
    [Control_Room.kicad_sch, Systems&Electronics.kicad_pcb, Systems&Electronics.kicad_sch]
2025-02-14 Communications board for RS485
    [Comms_Board.kicad_pcb, Comms_Board.kicad_sch]
2025-02-16 minor thermocouple shuffle
    [Systems&Electronics.kicad_pcb]
2025-02-16 trace and hole positioning updates
    [Systems&Electronics.kicad_pcb]
2025-02-16 feat(PCB): Final PCB Design
    [Systems&Electronics.kicad_pcb]
2025-05-06 Fixed some communications bugs with commands.
    Fixed shutdown not always working
    Fixed some commands failing to send
    [EngineFirmware1.2.ino, serialworker.h]
2025-05-09 Fixed a bug with communication
    [mainwindow.h]
2025-05-09 Minor communication bug fixes
    Fixed UI Slowdown on higher data rates
    [mainwindow.h, sensors.h]
2025-05-10 DataChart is working now.
    - Replace Combustion Chamber Chart with Communications Telemetry
    - Test and Test Some More
    - Full integration test once all the hardware is soldered
    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
    [mainwindow.h]
2025-11-21 Cold-Flow Tested Software
    [sensor-data.ods]
2025-12-18 Arduino Nano Servo Motor Controller
